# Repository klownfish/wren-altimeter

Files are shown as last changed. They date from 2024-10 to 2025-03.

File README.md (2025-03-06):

# Wren
Wren is an altimeter small enough to fit in a standard 18mm model rocket. It is designed to be assembled by JLCPCB for as low of a price as possible. The altitude, velocity and acceleration are sampled and saved at 50Hz. The battery should last for tens of hours while waiting for a launch and is charged through USB-C

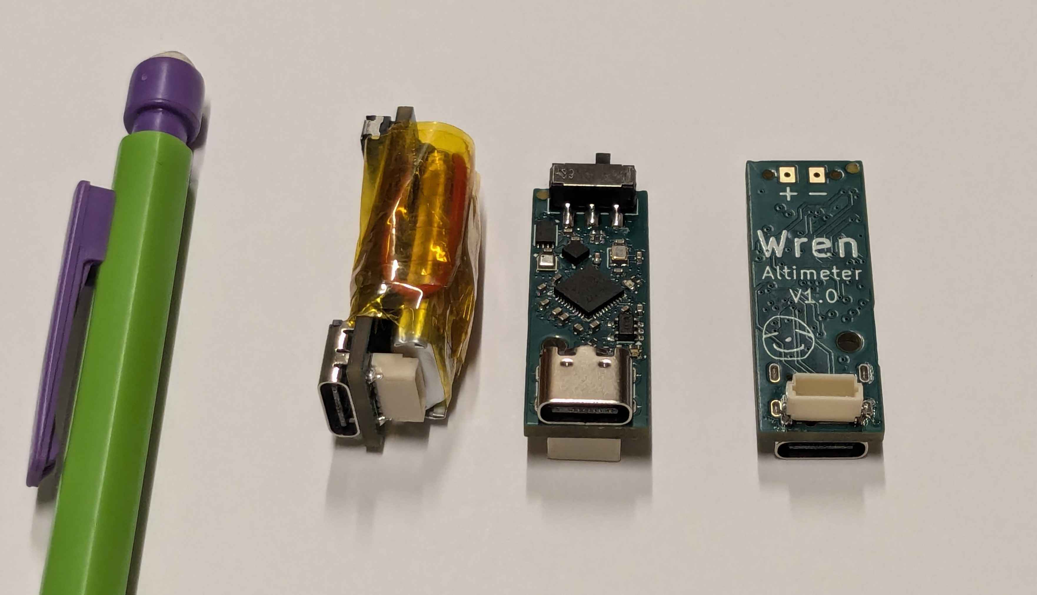
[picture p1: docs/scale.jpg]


## Hardware
A 12mm x 34mm 4 layer PCB, designed to only use components from JLCPCB's stock. Single sided assembly with only a debug connector and battery pads on the back.

1. **MCU:** A low-power nRF52833.

1. **Accelerometer:** A LIS2DH rotated 45° allowing it to measure accelerations up to 22.5G instead of the typical 16G limit.

1. **Barometer:** A BMP390 for altitude measurements.

1. **Flash Memory:** 4Mbit of onboard flash. Should log ~10 flights at 50Hz.

1. **Battery:** LiPo charging at 30mA.

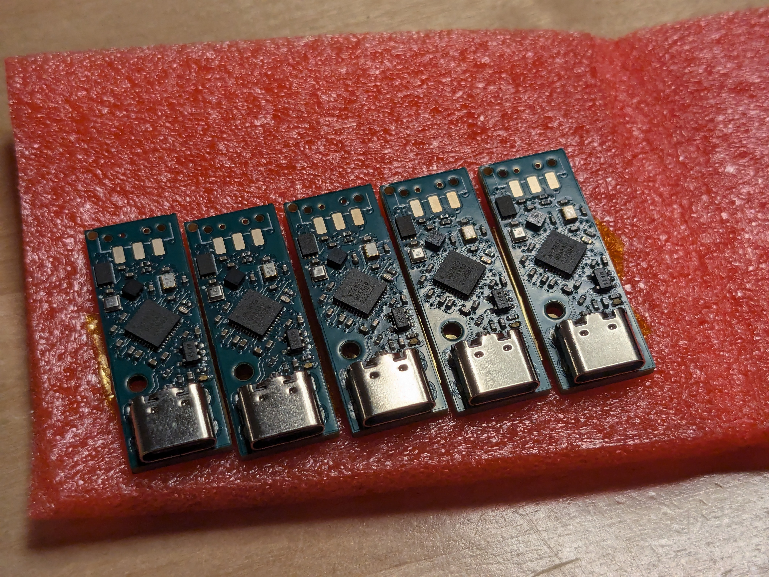
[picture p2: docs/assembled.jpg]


# Firmware

The onboard firmware is developed in Rust using the [Embassy](https://embassy.dev/) framework.

## Flashing the Firmware

### 1. Flash the Bootloader
Before flashing the firmware, you must first flash the bootloader. Navigate to the `firmware/bootloader/` directory and run:

```bash
cargo run --release
```

### 2. Flash the Firmware
Once the bootloader is installed, navigate to the `firmware/` directory and run the same command:

```bash
cargo run --release
```

> **Note:** You only need to flash the bootloader once unless you modify it.

## Updating via USB
Once the bootloader is flashed, you can update the firmware directly over USB.

### 1. Build the Firmware Binary
Generate a binary file suitable for flashing:

```bash
cargo objcopy --release -- -O binary firmware.bin
```

This will create `firmware.bin` in the current directory.

### 2. Upload the Firmware
1. **Connect the board** to a USB port.
2. **Run the firmware updater script:**

   ```bash
   python firmware_updater.py ../firmware/firmware.bin
   ```

3. **Power cycle the board** – The updater intercepts the boot process to load the new firmware.

## Testing
To run a native test build with mock drivers, use:

```bash
cargo run --target x86_64-unknown-linux-gnu
```

*(Or any other architecture that supports the Rust standard library.)*

---

# Software

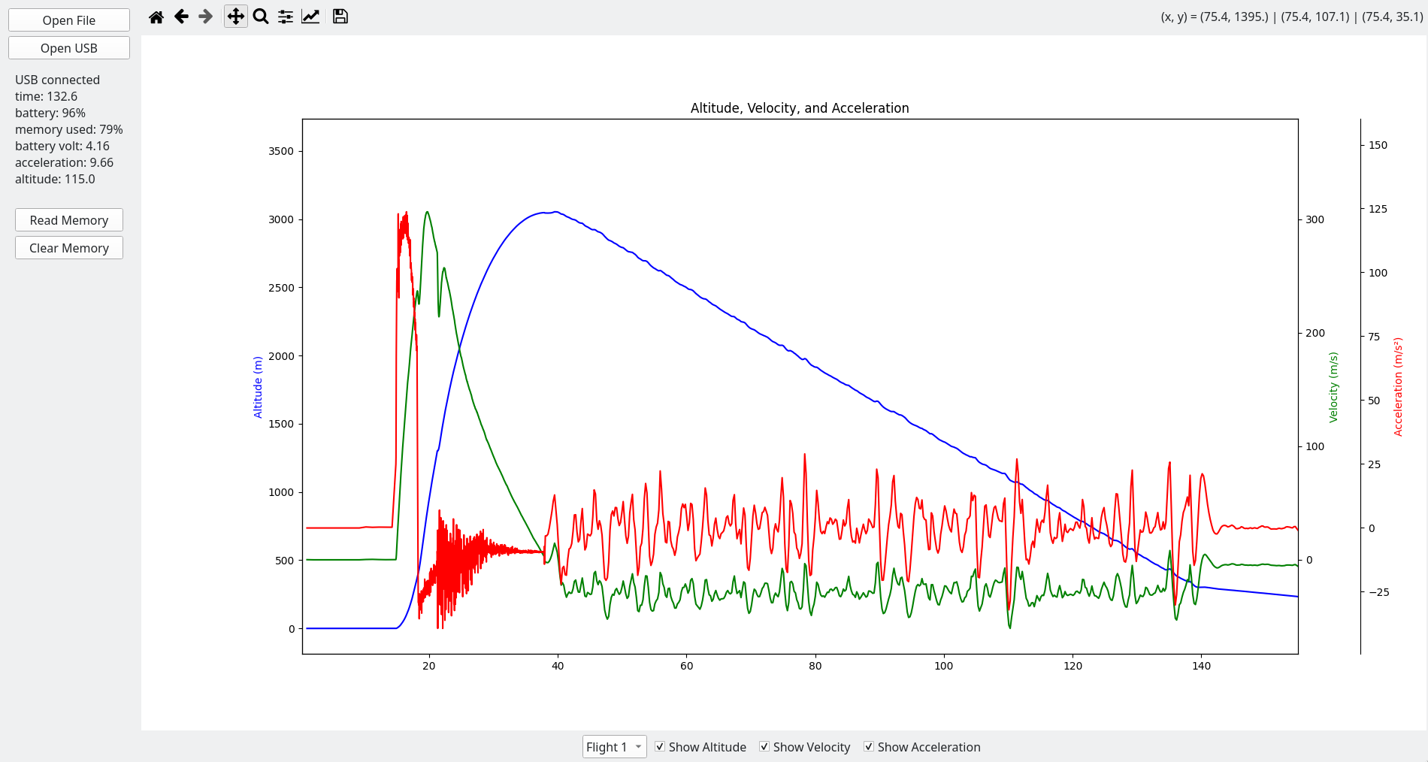
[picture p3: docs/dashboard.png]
Dashboard Interface


To fetch data and manage the altimeter, use the dashboard:

```bash
python dashboard/main.py
```

### WIP bluetooth version
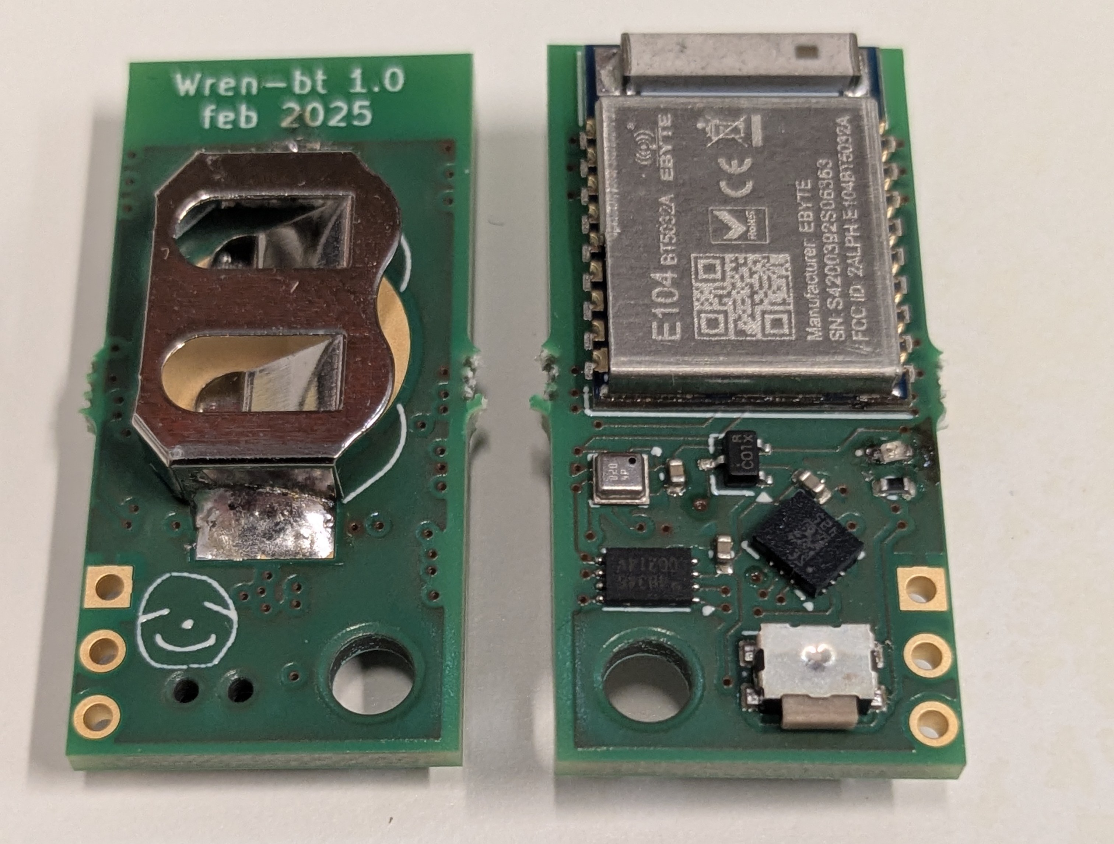
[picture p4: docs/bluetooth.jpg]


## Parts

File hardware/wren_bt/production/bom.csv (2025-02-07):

Designator | Footprint | Quantity | Value | LCSC Part #
C1, C2, C4 | 0402 | 3 | 0.1u | C1525
D1 | 0402 | 1 | red | C7420553
Q1 | SOT-323_SC-70 | 1 | Q_PMOS_GSD | C391640
R1 | 0402 | 1 | 510 | C25123
SW2 | SW_SPST_CK_KMS2xxGP | 1 | SW_Push_Shielded | C221703
U1 | E104-BT5032A_BYT | 1 | E104-BT5032A | C518912
U2 | XDCR_BMP390L | 1 | BMP390L
U3 | Winbond_USON-8-1EP_3x2mm_P0.5mm_EP0.2x1.6mm | 1 | W25X40CLUXIG | C401661
U5 | LGA-14_3x2.5mm_P0.5mm_LayoutBorder3x4y | 1 | LSM6DS3 | C95230

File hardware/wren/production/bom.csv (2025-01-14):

Designator | Footprint | Quantity | Value | LCSC Part #
C1, C11, C18, C3, C4, C5, C7 | 0402 | 7 | 0.1u | C1525
C10, C12, C13, C17, C2, C9 | 0402 | 6 | 4.7u | C23733
C14 | 0402 | 1 | 1u | C52923
C15, C16 | 0402 | 2 | 10p | C32949
C19 | 0805 | 1 | 33u | C342635
C6 | 0402 | 1 | 100p | C1546
D1 | 0402 | 1 | blue | C917189
D2 | 0402 | 1 | red | C7420553
J1 | USB_C_Receptacle_GCT_USB4105-xx-A_16P_TopMnt_Horizontal | 1 | USB_C_Receptacle_USB2.0_16P | C2765186
R1, R3 | 0402 | 2 | 5.1k | C25905
R2 | 0402 | 1 | 100k | C25741
R5, R8 | 0402 | 2 | 51k | C25794
R6, R7 | 0402 | 2 | 470 | C25117
U1 | QFN-40-1EP_5x5mm_P0.4mm_EP3.6x3.6mm | 1 | nRF52833_QDxx | C2895249
U2 | SOT-23-5 | 1 | MCP73832T-2 | C38066
U3 | XDCR_BMP390L | 1 | BMP390L | C2684802
U4 | Winbond_USON-8-1EP_3x2mm_P0.5mm_EP0.2x1.6mm | 1 | W25X40CLUXIG | C401661
U5 | LGA-14_2x2mm_P0.35mm_LayoutBorder3x4y | 1 | LIS2DH | C155670
Y1 | Crystal_SMD_2016-4Pin_2.0x1.6mm | 1 | 32MHz | C388796

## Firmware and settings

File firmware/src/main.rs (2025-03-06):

#![cfg_attr(target_os = "none", no_std)]
#![cfg_attr(target_os = "none", no_main)]

#[allow(unused_imports)]
#[cfg(target_os = "none")]
use defmt::{debug, error, info, trace, warn};
#[cfg(target_os = "none")]
use dummy_pin::DummyPin;
#[cfg(target_os = "none")]
use embassy_embedded_hal::shared_bus::asynch::spi::SpiDevice;
#[cfg(target_os = "none")]
use embassy_nrf::gpio::{Level, Output, OutputDrive};
#[cfg(target_os = "none")]
use embassy_nrf::peripherals::SPI2;
#[cfg(target_os = "none")]
use embassy_nrf::saadc;
#[cfg(target_os = "none")]
use embassy_nrf::{bind_interrupts, peripherals, spim, wdt};
#[cfg(target_os = "none")]
#[cfg(feature = "wren")]
use embassy_nrf::usb;
#[cfg(target_os = "none")]
use embassy_time::Delay;
#[cfg(target_os = "none")]
use embassy_time::with_timeout;
#[cfg(target_os = "none")]
use embassy_nrf::pac;
#[cfg(target_os = "none")]
use libm::powf;
#[cfg(target_os = "none")]
use {defmt_rtt as _, panic_probe as _};


#[allow(unused_imports)]
#[cfg(not(target_os = "none"))]
use log::{debug, error, info, trace, warn};
#[cfg(not(target_os = "none"))]
use env_logger;

use embassy_executor::Spawner;
use embassy_sync::blocking_mutex::raw::ThreadModeRawMutex;
use embassy_sync::mutex::Mutex;
use embassy_time::Timer;
use flash_writer::FlashWriter;
use platform::{AccelerometerType, BarometerType, FlashMemoryType};
use static_cell::StaticCell;


mod flash_writer;
mod flight_sm;
mod flight_task;
mod kalman;
mod platform;

#[cfg(target_os = "none")]
#[cfg(feature = "wren")]
mod usb_handler;

#[allow(unused)]
struct WrenState {
    battery_voltage: f32,
    acceleration: f32,
    altitude: f32,
}

#[cfg(all(feature = "wren", feature = "wren-bt"))]
compile_error!("Features 'wren' and 'wren-bt' are mutually exclusive!");

#[cfg(target_os = "none")]
bind_interrupts!(struct Irqs {
    #[cfg(feature = "wren")]
    USBD => usb::InterruptHandler<peripherals::USBD>;
    #[cfg(feature = "wren")]
    CLOCK_POWER => usb::vbus_detect::InterruptHandler;

    SPI2 => spim::InterruptHandler<SPI2>;
    SAADC => saadc::InterruptHandler;
});

#[cfg(all(target_os = "none", feature = "wren-bt"))]
#[cfg_attr(all(target_os = "none", feature = "wren-bt"), embassy_executor::main)]
async fn main_FAGOOT(spawner: Spawner) {
    let mut nrf_config = embassy_nrf::config::Config::default();
    nrf_config.hfclk_source = embassy_nrf::config::HfclkSource::ExternalXtal;
    let p = embassy_nrf::init(nrf_config);

    info!("Starting Wren-bt {}", env!("CARGO_PKG_VERSION"));
    info!("Enabling ext hfosc...");
    pac::CLOCK.tasks_hfclkstart().write_value(1);
    while pac::CLOCK.events_hfclkstarted().read() != 1 {}
    Timer::after_millis(100).await;

    let mut pwr_pin = Output::new(p.P0_07, Level::High, OutputDrive::HighDrive);
    let baro_cs = Output::new(p.P0_25, Level::High, OutputDrive::HighDrive);
    let acc_cs = Output::new(p.P0_10, Level::High, OutputDrive::HighDrive);
    let flash_cs = Output::new(p.P0_26, Level::High, OutputDrive::HighDrive);

    pwr_pin.set_high();
    Timer::after_millis(500).await;

    let mut spi_config = spim::Config::default();
    spi_config.frequency = spim::Frequency::M1;

    static SPI_BUS: StaticCell<Mutex<ThreadModeRawMutex, spim::Spim<peripherals::SPI2>>> = StaticCell::new();
    let spi = spim::Spim::new(p.SPI2, Irqs, p.P0_05, p.P0_04, p.P0_03, spi_config);

    let spi_bus = Mutex::new(spi);
    let spi_bus = SPI_BUS.init(spi_bus);

    let baro_spi_device: SpiDevice<'_, ThreadModeRawMutex, spim::Spim<'_, SPI2>, Output<'_>> =
        SpiDevice::new(spi_bus, baro_cs);
    let acc_spi_device = SpiDevice::new(spi_bus, acc_cs);
    let flash_spi_device = SpiDevice::new(spi_bus, flash_cs);

    loop {
        Timer::after_millis(100).await;
    }
}

#[cfg(all(target_os = "none", feature = "wren"))]
#[cfg_attr(all(target_os = "none", feature = "wren"), embassy_executor::main)]
async fn main_RETADSAD(spawner: Spawner) {
    let mut nrf_config = embassy_nrf::config::Config::default();
    nrf_config.hfclk_source = embassy_nrf::config::HfclkSource::ExternalXtal;
    nrf_config.dcdc.reg0_voltage = Some(embassy_nrf::config::Reg0Voltage::_2V4); //flash memory is not rated for 1v8 apparently
    nrf_config.dcdc.reg1 = false;
    let p = embassy_nrf::init(nrf_config);

    info!("Starting Wren {}", env!("CARGO_PKG_VERSION"));

    let wdt_config = wdt::Config::try_new(&p.WDT).unwrap();
    let (_wdt, [mut wdt_handle]) = match wdt::Watchdog::try_new(p.WDT, wdt_config) {
        Ok(x) => x,
        Err(_) => {
            // Watchdog already active with the wrong number of handles, waiting for it to timeout...
            loop {
                cortex_m::asm::wfe();
            }
        }
    };


    info!("Enabling ext hfosc...");
    pac::CLOCK.tasks_hfclkstart().write_value(1);
    while pac::CLOCK.events_hfclkstarted().read() != 1 {}
    Timer::after_millis(100).await;

    let mut led_pin = Output::new(p.P0_09, Level::High, OutputDrive::HighDrive);
    let mut pwr_pin = Output::new(p.P0_01, Level::High, OutputDrive::HighDrive);
    let baro_cs = Output::new(p.P0_30, Level::High, OutputDrive::HighDrive);
    let acc_cs = Output::new(p.P0_03, Level::High, OutputDrive::HighDrive);
    let flash_cs = Output::new(p.P0_10, Level::High, OutputDrive::HighDrive);

    pwr_pin.set_high();
    led_pin.set_high();
    Timer::after_millis(500).await;

    let mut spi_config = spim::Config::default();
    spi_config.frequency = spim::Frequency::M1;

    static SPI_BUS: StaticCell<Mutex<ThreadModeRawMutex, spim::Spim<peripherals::SPI2>>> = StaticCell::new();
    let spi = spim::Spim::new(p.SPI2, Irqs, p.P0_29, p.P0_02, p.P0_28, spi_config);

    let spi_bus = Mutex::new(spi);
    let spi_bus = SPI_BUS.init(spi_bus);

    let baro_spi_device: SpiDevice<'_, ThreadModeRawMutex, spim::Spim<'_, SPI2>, Output<'_>> =
        SpiDevice::new(spi_bus, baro_cs);
    let acc_spi_device = SpiDevice::new(spi_bus, acc_cs);
    let flash_spi_device = SpiDevice::new(spi_bus, flash_cs);

    let usb_driver = usb::Driver::new(p.USBD, Irqs, usb::vbus_detect::HardwareVbusDetect::new(Irqs));

    let flash = FlashMemoryType::new(flash_spi_device, DummyPin::new_low(), DummyPin::new_low()).unwrap();
    // flash.erase_all().await.expect("couldn't erase flash");

    let mut baro: BarometerType = bmp388::Bmp388::new(baro_spi_device, &mut Delay)
        .await
        .expect("initializing baro failed");
    baro.set_oversampling(bmp388::config::OversamplingConfig {
        osr_pressure: bmp388::Oversampling::x8,
        osr_temperature: bmp388::Oversampling::x1,
    })
    .await
    .expect("setting baro oversample failed");
    baro.set_sampling_rate(bmp388::SamplingRate::ms20)
        .await
        .expect("setting baro sample rate failed");
    baro.set_filter(bmp388::Filter::c1).await.expect("set baro filter failed");
    let power_control = bmp388::PowerControl {
        mode: bmp388::PowerMode::Normal,
        pressure_enable: true,
        temperature_enable: true,
    };
    baro.set_power_control(power_control).await.expect("couldn't set power control");

    let mut acc = AccelerometerType::new(acc_spi_device).await.expect("couldn't initialize acc");
    acc.set_bdu(true).await.expect("coudln't set bdu");
    acc.enabled_adcs().await.expect("coudln't enable adc");
    acc.enable_temp(true).await.expect("couldn't enable temp");
    acc.enable_axis((true, true, true)).await.expect("couldn't set acc axis");
    acc.set_mode(lis2dh12::Mode::HighResolution)
        .await
        .expect("couldn't set acc mode");
    acc.set_fs(lis2dh12::FullScale::G16).await.expect("couldn't set acc scale");
    acc.set_odr(lis2dh12::Odr::Hz100).await.expect("couldn't set acc ODR");

    static FLASH: StaticCell<Mutex<ThreadModeRawMutex, FlashWriter>> = StaticCell::new();
    let flash = FLASH.init(Mutex::new(FlashWriter::new(flash).await.unwrap()));

    static WREN: StaticCell<Mutex<ThreadModeRawMutex, WrenState>> = StaticCell::new();
    let wren = WrenState {
        altitude: 0.0,
        acceleration: 0.0,
        battery_voltage: 0.0,
    };
    let wren = WREN.init(Mutex::new(wren));

    spawner.spawn(flight_task::flight_task(baro, acc, flash, wren)).unwrap();

    spawner.spawn(usb_handler::usb_task(spawner, usb_driver, flash, wren)).unwrap();



    let mut adc_config = saadc::Config::default();
    adc_config.oversample = saadc::Oversample::OVER256X;
    adc_config.resolution = saadc::Resolution::_14BIT;
    let mut channel_config = saadc::ChannelConfig::single_ended(p.P0_04);
    channel_config.reference = saadc::Reference::INTERNAL; // 0.6V
    channel_config.gain = saadc::Gain::GAIN1_3; // 0.6V * 3 = 1.8V
    channel_config.time = saadc::Time::_40US; // high input resistance in the divider
    let saadc: saadc::Saadc<'_, 1> = saadc::Saadc::new(p.SAADC, Irqs, adc_config, [channel_config]);
    saadc.calibrate().await;

    #[embassy_executor::task]
    async fn adc_task(mut saadc: saadc::Saadc<'static, 1>, wren: &'static Mutex<ThreadModeRawMutex, WrenState>) {
        loop {
            let mut adc_buf = [0_i16; 1];
            saadc.sample(&mut adc_buf).await;
            let volt = adc_buf[0] as f32 / (powf(2.0, 14.0) - 1.0) * 1.8 * 151.0 / 51.0;
            {
                let mut wren = wren.lock().await;
                wren.battery_voltage = volt;
            };
            Timer::after_millis(250).await;
        }
    }
    spawner.spawn(adc_task(saadc, wren)).unwrap();

    let mut index = flash.lock().await.get_index();
    let mut size = flash.lock().await.get_size();
    loop {
        match with_timeout(embassy_time::Duration::from_millis(100), flash.lock()).await {
            Ok(flash) => {
                index = flash.get_index();
                size = flash.get_size();
            },
            Err(_) => {}
        }
        if index < 1 {
            index = 1
        }

        let to_blink = 4 - (((index - 1) as f32 / size as f32) * 4.0) as u32;
        for _ in 0..to_blink {
            led_pin.set_high();
            Timer::after_millis(200).await;
            led_pin.set_low();
            Timer::after_millis(200).await;
        }
        Timer::after_millis(1000).await;
        wdt_handle.pet();
    }
}

#[cfg(not(target_os = "none"))]
#[embassy_executor::task]
async fn init_native(spawner: Spawner) {
    let baro = BarometerType::new();
    let accel = AccelerometerType::new();
    let flash = FlashMemoryType::new();

    static FLASH: StaticCell<Mutex<ThreadModeRawMutex, FlashWriter>> = StaticCell::new();
    let flash = FLASH.init(Mutex::new(FlashWriter::new(flash).await.unwrap()));

    static WREN: StaticCell<Mutex<ThreadModeRawMutex, WrenState>> = StaticCell::new();
    let wren = WrenState {
        altitude: 0.0,
        acceleration: 0.0,
        battery_voltage: 0.0,
    };
    let wren = WREN.init(Mutex::new(wren));
    spawner.spawn(flight_task::flight_task(baro, accel, flash, wren)).unwrap();
    loop {
        Timer::after_millis(500).await;
    }
}

#[cfg(not(target_os = "none"))]
fn main() {
    env_logger::init();
    use embassy_executor::Executor;
    static EXECUTOR: StaticCell<Executor> = StaticCell::new();
    let executor = EXECUTOR.init(Executor::new());
    executor.run(|spawner| {
        spawner.spawn(init_native(spawner)).unwrap();
    });
}

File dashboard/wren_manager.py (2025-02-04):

import struct
from collections import defaultdict
import serial
import serial.tools.list_ports
import json

IdVoltage = 1
IdTelemetry = 2
IdState = 3
IdPowerOn = 4
IdDebug = 5
IdTime = 6

class TimeSeries:
    def __init__(self):
        self.x = []
        self.y = []

class WrenManager():
    def __init__(self):
        self.splits = []
        self.usb_is_open = False

        self.altitude = 0
        self.voltage = 0
        self.battery_voltage = 0
        self.battery_percent = 0
        self.acceleration = 0
        self.flash_used = 100
        self.time = 0

    def lipo_charge_percentage(self, voltage):
        voltage_to_percent = [
            (3.0, 0),     # 3.0V -> 0% (fully discharged)
            (3.2, 10),    # 3.2V -> 10%
            (3.4, 20),    # 3.4V -> 20%
            (3.6, 40),    # 3.6V -> 40%
            (3.8, 60),    # 3.8V -> 60%
            (4.0, 80),    # 4.0V -> 80%
            (4.2, 100),   # 4.2V -> 100% (fully charged)
        ]

        if voltage <= 3.0:
            return 0.0
        if voltage >= 4.2:
            return 100.0

        for i in range(len(voltage_to_percent) - 1):
            v1, p1 = voltage_to_percent[i]
            v2, p2 = voltage_to_percent[i + 1]
            if v1 <= voltage <= v2:
                percentage = p1 + (p2 - p1) * (voltage - v1) / (v2 - v1)
                return round(percentage, 1)

        # Default fallback (shouldn't be reached)
        return 0.0

    def open_file(self, path):
        f = open(path, "rb")
        buf = f.read()
        if path.endswith(".csv"):
            self.parse_csv(buf)
        else:
            self.parse_binary(buf)

    def open_usb(self):
        ports = serial.tools.list_ports.comports()

        for port in ports:
            try:
                # Open serial connection
                ser = serial.Serial(port.device, timeout=30)
                ser.read_all()
                ser.write(b"wren?\n")  # Send query to device

                # Read response
                response = ser.readline().strip().decode("utf-8")
                if response == "wren!":
                    self.ser = ser  # Save the serial connection for future use
                    self.usb_is_open = True
                    print("found usb port")
                    return
                else:
                    print(response)
                ser.close()  # Close the port if the response is incorrect
            except (serial.SerialException, UnicodeDecodeError) as e:
                print(f"Error checking port {port.device}: {e}")
        self.usb_open = False
        print("did not find")

    def fetch_status(self):
        self.ser.write(b"get_status\n")
        response = self.ser.readline().strip().decode("utf-8")

        parsed = json.loads(response)
        self.flash_used = parsed["flash_used"] / parsed["flash_size"]
        self.battery_voltage = parsed["volt"]
        self.battery_percent = self.lipo_charge_percentage(self.battery_voltage)
        self.time = parsed["time"] / 1000
        self.acceleration = parsed["acceleration"]
        self.altitude = parsed["altitude"]

    def read_flash(self):
        self.ser.write(b"read_flash\n")
        response = self.ser.readline().strip().decode("utf-8")
        parsed = json.loads(response)
        binary_length = parsed["length"]
        print(binary_length)
        buf = self.ser.read(binary_length)
        print(len(buf))
        if len(buf) == binary_length:
            return buf
        else:
            print("bad binary file")

    def clear_flash(self):
        self.ser.write(b"clear_flash\n")

    def parse_binary(self, buf):
        current_time = 0
        offset_time = 0
        just_powered_on = True # set this to true to not initialize
        last_raw_time = 0
        index = 0
        split_index = 0
        current_dict = defaultdict(lambda: TimeSeries())
        while True:
            if index == len(buf):
                if "boost" in current_dict["state"].y:
                    self.splits.append(current_dict)
                break
            id = buf[index]
            index += 1
            if id == IdPowerOn: # power on
                if just_powered_on == False:
                    if "boost" in current_dict["state"].y:
                        self.splits.append(current_dict)
                    current_dict = defaultdict(lambda: TimeSeries())
                    just_powered_on = True
                continue

            just_powered_on = False
            if id == IdTelemetry:
                (alt_raw, vel_raw, acc_raw) = struct.unpack_from("<HHH", buf, index)
                index += struct.calcsize("<HHH")
                alt = alt_raw / 4
                vel = vel_raw / 100 - 100
                acc = acc_raw / 200 - 200

                current_dict["altitude"].x.append(current_time)
                current_dict["altitude"].y.append(alt)

                current_dict["velocity"].x.append(current_time)
                current_dict["velocity"].y.append(vel)

                current_dict["acceleration"].x.append(current_time)
                current_dict["acceleration"].y.append(acc)


            elif id == IdState:
                (state,) = struct.unpack_from("<B", buf, index)
                index += struct.calcsize("<B")

                state_to_name = {
                    0: "idle",
                    1: "maybe_launched",
                    2: "boost",
                    3: "coast",
                    4: "descent",
                }

                name = state_to_name[state]
                current_dict["state"].x.append(current_time)
                current_dict["state"].y.append(name)

            elif id == IdVoltage:
                (volt_raw,) = struct.unpack_from("<H", buf, index)
                index += struct.calcsize("<H")
                volt = volt_raw / 1000
                current_dict["volt"].x.append(current_time)
                current_dict["volt"].y.append(volt)

            elif id == IdDebug:
                index += struct.calcsize("<fffdI")

            elif id == IdTime:
                (time,) = struct.unpack_from("<I", buf, index)
                index += struct.calcsize("<I")
                current_time = time / 1000.0

            else:
                print("invalid id", id)

if __name__ == "__main__":
    wren = WrenManager()
    wren.open_file("/tmp/wren_flash.bin")
    wren.open_usb()
    wren.fetch_status()
    wren.read_flash()

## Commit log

2024-10-07 add LCSC BOM
    [altimeter.kicad_pcb, altimeter.kicad_sch]
2024-10-10 ordered version
    [altimeter.kicad_pcb, altimeter.kicad_sch, bom.csv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]
2024-10-11 actually ordered version
    [altimeter.kicad_pcb, positions.csv]
2024-10-14 prepare for firmware
    [altimeter.kicad_pcb, altimeter.kicad_sch, bom.csv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]
2024-10-18 initial bmp388 driver
2024-10-20 add kalman filter
2024-11-03 fix baro spi read
    [lib.rs]
2024-11-03 manually set regulator voltage
2024-11-10 fix kalman filter variable measurement dimension
    [main.rs]
2025-01-06 rewrite for native simulation
    [skyward_baro.csv]
2025-01-11 add adc and state
2025-01-14 new hardware revision
    [altimeter.kicad_pcb, altimeter.kicad_sch, bom.csv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]
2025-01-14 ordered v1.1
    [bom.csv]
2025-01-28 move regulator into embassy
2025-02-07 Add bluetooth board
    [altimeter.kicad_pcb, altimeter.kicad_sch, altimeter2.kicad_pcb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]
2025-02-11 orderer v1.0-bt
    [altimeter2.kicad_pcb, designators.csv]
